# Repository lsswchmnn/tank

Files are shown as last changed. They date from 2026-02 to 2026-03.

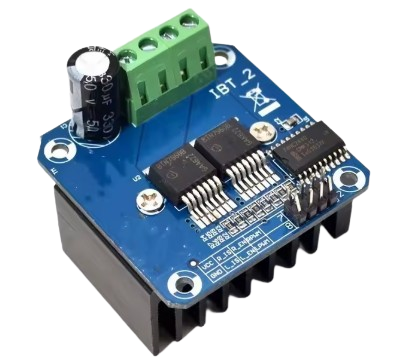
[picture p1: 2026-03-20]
Präsentation/h_brücke.png

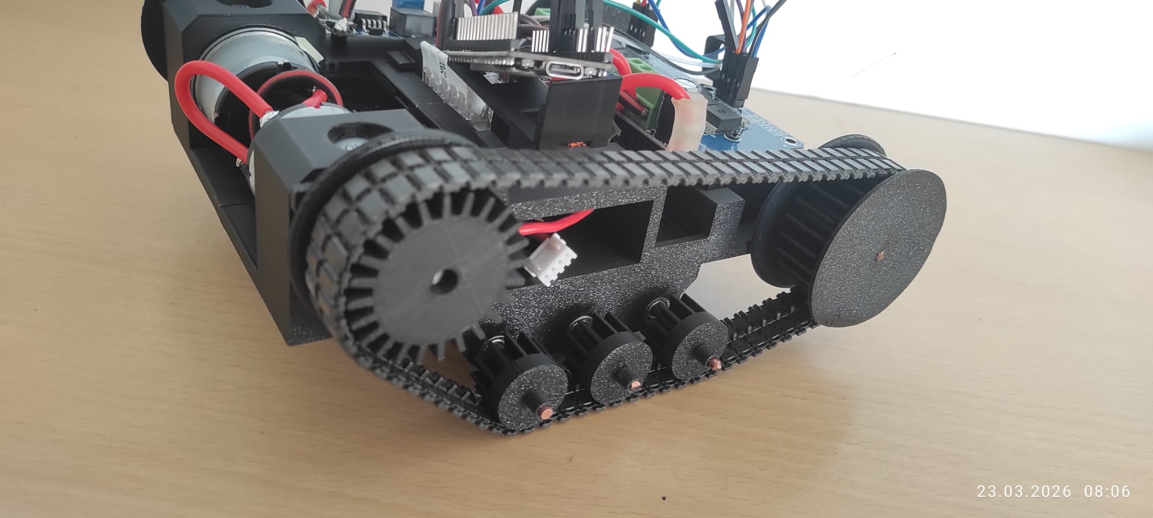
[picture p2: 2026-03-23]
Präsentation/WhatsApp Image 2026-03-23 at 09.37.09.jpeg

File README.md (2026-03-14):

# RC-Panzer

## Zeitplan:

12.Feb. - 27.März: Arbeit an (ca. 4 Wochen (exkl. Ferien)

16. März: Austausch zum Stand der Projekte, Problembesprechung

23. März: Präsentation / Abgabe des Semesterprojektes 

## ToDo:

- Teile bestellen

- 3D-Modell erstellen

- Schaltplan erstellen

- Lauffähiges Grundmodell bauen

## Weitere Teile:

- ESP32(1x 4,69 EUR),
- Motordriver (2x ins.: 6,98 EUR), 
- BUCK-Converter (2x ins.: 1,89 EUR), 
- Motoren (2x ins.: 13,89 EUR), 
- Akku(1x 17,49 EUR) 

### == 46,03 EUR (Bezahlt)

- AWG 14 Kabel (1x 1,75 EUR),
- 3x200mm Metallachsen (1x 4,48EUR),
- 20pcs Kugellager (1x 2,09 EUR)

### == 8,32 EUR (nicht bezahlt) 

- Wago Klemmen == 4,20 EUR (nicht bezahlt) 
- Ketten == 10,98 EUR (nicht bezahlt)
- Jumperkabel == 5,94 EUR (nicht bezahlt)

### == 21,12 EUR (nicht bezahlt)

- 3x300mm (1x 3,12 EUR)
- Schrumpfschläuche 164 pcs. (1x 2,79 EUR)
- AWG 14 Kabel (1x 3,31 EUR)

### == 9, 22 EUR (nicht bezahlt)

## INSGESAMT: 84,69 EUR

- Panzerketten: https://www.modellbau-seidel.de/index.php?firma=Tamiya&best=0003778 (1,7cm x 42,5cm) ODER https://www.modellbau-seidel.de/index.php?firma=Tamiya&best=0443086 (1,5cm x 35cm)

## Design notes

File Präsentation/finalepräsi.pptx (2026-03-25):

## Kettenfahrzeug

Semesterprojekt von Lasse, Hossein, Julian

## Inhaltsverzeichnis

1. Konstruktion und Planung
2. Elektronik und Verkabelung
3. Programmierung
4. Allgemeines

## Konstruktion

Lasse

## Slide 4

Rahmen

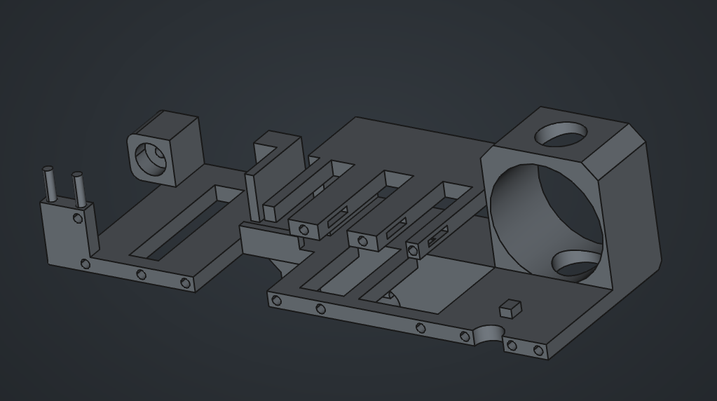
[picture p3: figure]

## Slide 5

Weitere Teile

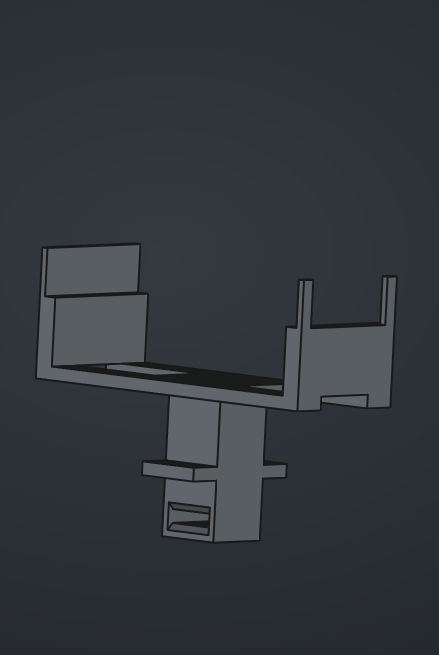
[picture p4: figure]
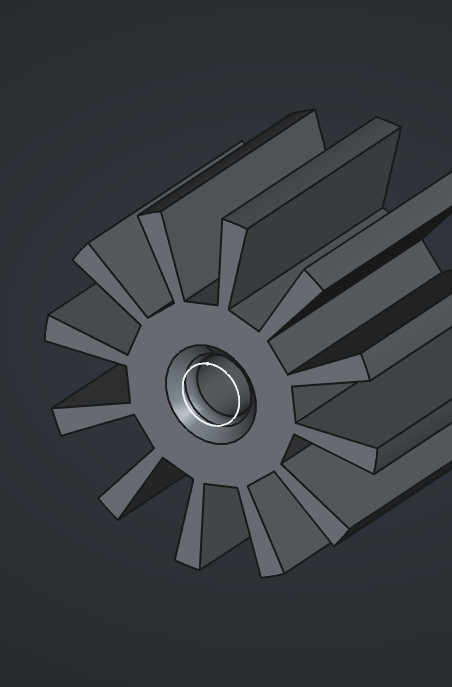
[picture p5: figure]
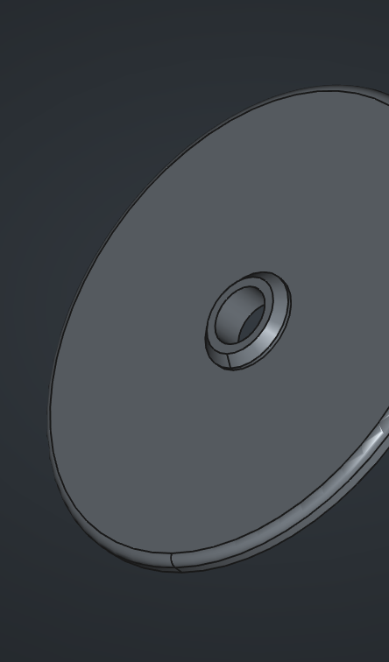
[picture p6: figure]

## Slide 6

Kabelmanagement

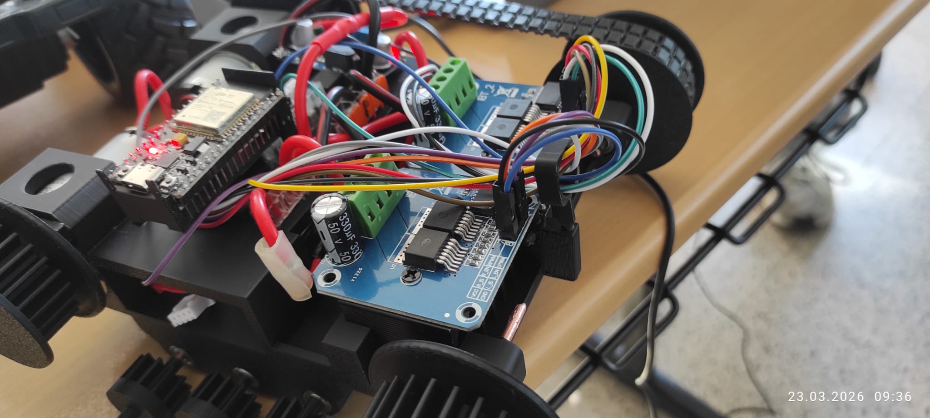
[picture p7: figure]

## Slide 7

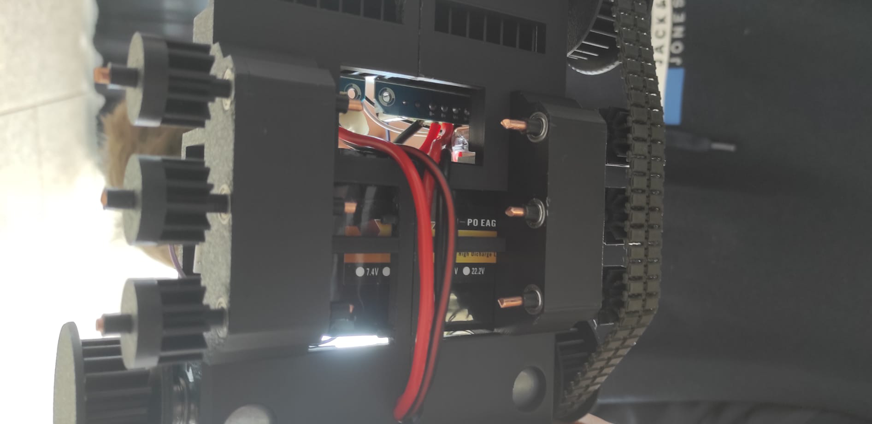
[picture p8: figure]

Kabelmanagement

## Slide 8

Fahrgestell

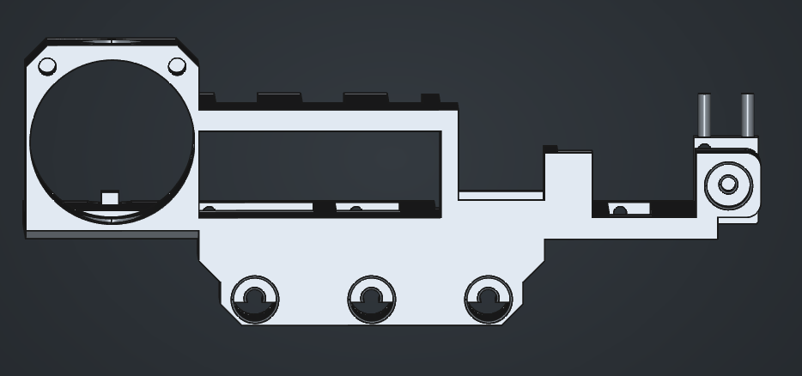
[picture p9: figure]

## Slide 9

Fahrgestell


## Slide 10

Zwischenfazit

Negativ
- Viele Testdrucke notwendig (Material- und Zeitaufwand)
- Millimeter können ein Modell unbrauchbar machen

Positiv
- Doppeltes Fahrgestell
- Modulares System mit vielen externen Teilen
- Flexibilität des Materials ist ein Vorteil

Allgemein
- Frühe durchdachte Planung lohnt sich
- 3D-Druck-Ungenauigkeiten antizipieren
- Improvisation ist oft notwendig

## Elektronik

Julian

## Elektronik

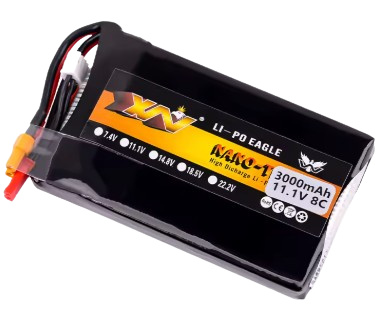
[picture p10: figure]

- 11.1V 3500mAh - Akku
- 2x BTS7960 43A – H-Brücke
- 2x JGB37-520 12V Motor
- LM2596 – Buck-Converter
- ESP32 Dev-Module (38 Pins)

*Alle aufgeführten Bauteile stammen von Aliexpress

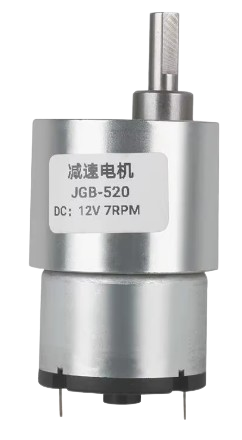
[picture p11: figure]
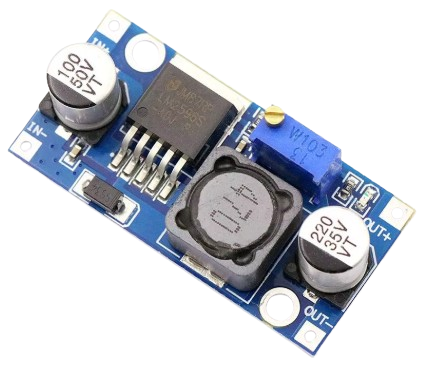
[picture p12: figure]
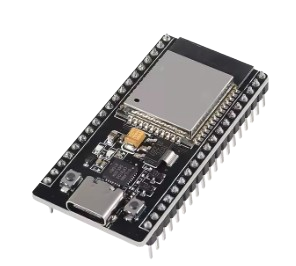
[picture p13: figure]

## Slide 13

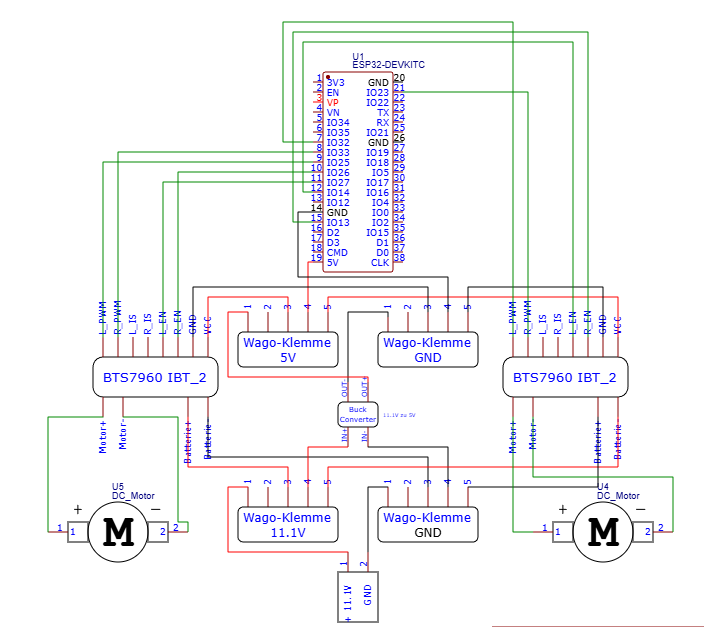
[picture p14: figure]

https://easyeda.com

## Programmierung

Hossein

## Programmierung

1. Mit ChatGPT ein Überblick erstellt (nötige Tools usw.)
2. Verbindung zwischen ESP32 und PS5 Controller (Bluepad32)
3. Schnittstelle zwischen Elektronik und Code

## 1. Schritt

1. Ziel definiert: Was soll der Roboter können?
2. KI gefragt (z.B. ChatGPT/Claude): Weche Komponenten brauche ich? Welche Bibliotheken? Welcher Ansatz?
3. Grobe Architektur skizziert: ESP32 -> Bluetooth -> PS5 Controller -> Motorsteuerung
4. Offene Fragen gesammelt: Was muss ich noch recherchieren?

## 2. Schritt

1. Youtube & Dokumentation (Bluepad32) als Einstieg
2. Ersten Prototyp erstellt & getestet
3. Stabile BT-Verbindung ohne MAC-Adresse
4. Alle Eingaben live auslesbar (Buttons, Achsen, Trigger)
5. Problem erkannt: Stick Drift / Rauschen bei Nullstellung
6. Lösung: Deadzone + Komplettauslenkung definiert

## 3. Schritt

1. Verbindungs-Code als Basis genommen & erweitert
2. Achsenwerte auf Motorgeschwindigkeit gemappt
3. Deadzone -> Motoren stehen still
4. Komplettauslenkung -> Maximale Motorleistung
5. Richtungssteuerung implementiert

## Code

1. Bibliotheken einbinden
2. Konstanten definieren
3. Controller Array
4. Callback Funktion
5. Setup()
6. Loop()

## Bibliotheken

Bluepad32.h :
Übernahme der Bluetooth Protokolle

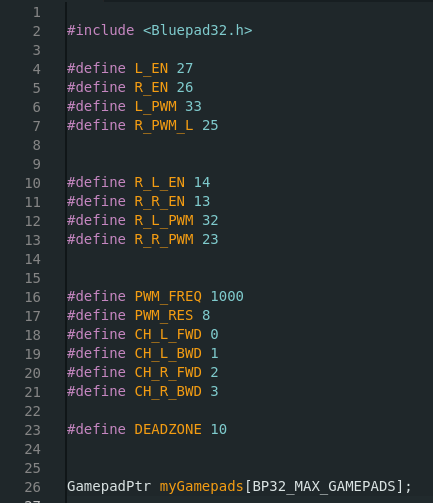
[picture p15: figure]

## Konstanten definieren

Definition:
- Verbindung BTS7960 mit ESP32
- PWM Frequenz
- PWM Resolution
- LEDC Kanäle
- Deadzone

## Controller Array

Gameptr-> Pointer
- Speicheradresse der Controller Daten
BP32_MAX_GAMEPADS
- Array

## Callback Funktion

- Aufruf der Funktion -> Controller verbunden
- FoundEmptySlot -> Reminder
- Zählschleife
- Nullptr -> Nullpointer
- Aufruf der Eigenschaften des Controllers
- Controller gefunden-> Schleife wird beendet

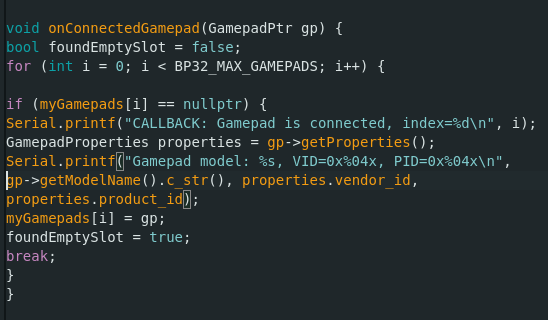
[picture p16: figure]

## Callback Funktion

- prüft ob der Slot gefunden wurde
- Slot wird geleert
- Schleife beendet

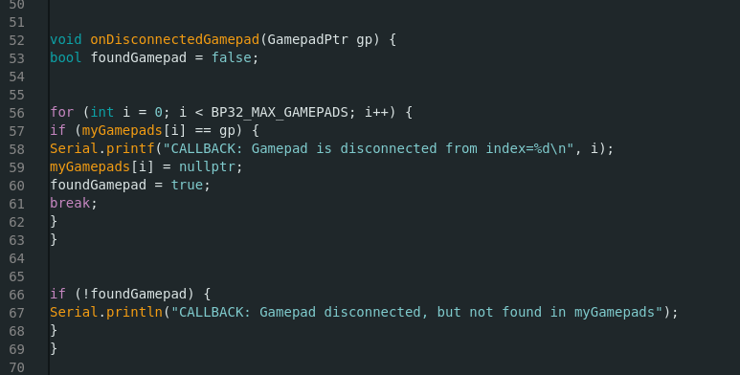
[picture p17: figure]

## Setup()

- Speichert wenn sich der Controller verbindet/ trennt

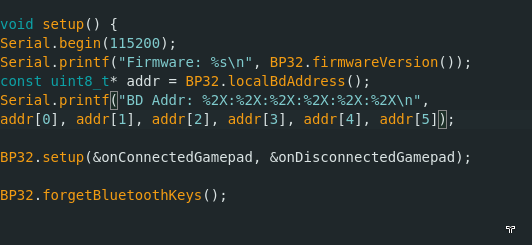
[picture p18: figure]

## PINS, PWM & LEDC

- Pin 27 als Ausgang
  - Setzt Pin auf HIGH(3,3V)
- LEDC Kanäle werden konfiguriert
- Kanal 0 wird mit Pin 33 verbunden

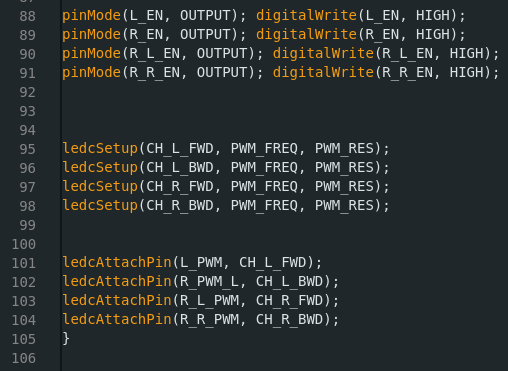
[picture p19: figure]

## loop

- ständiges Update
- Nach belegten Slot suchen -> Umbennenung -> myGamepad
- Doppelprüfung
  - Controller im Slot
  - Controller verbunden
- Werte aus den Sticks ablesen -> Methode axis -> myGamepad

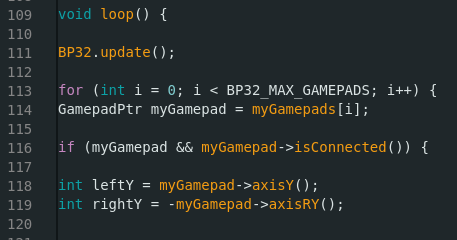
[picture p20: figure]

## Motorsteuerung

- Werte von Controller in PWM Werte umwandeln
- Vorwärts
  - CH_L_FWD speed
- Rückwärts
  - CH_L_BWD speed

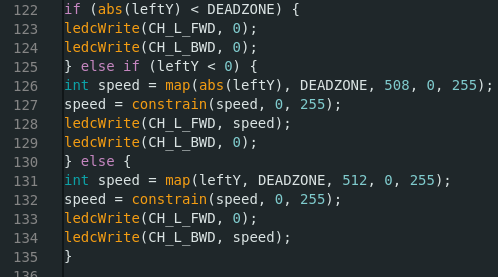
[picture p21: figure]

## Allgemeines

## Allgemeines

- Github als Kommunikationsplattform
- Ungelöste Probleme
- Arbeitsteilung

## Quellen

Code Dokumentation:
https://bluepad32.readthedocs.io/en/latest/plat_arduino/
Zusätzliche Board URL‘s:
https://raw.githubusercontent.com/espressif/arduino-esp32/gh-pages/package_esp32_index.json
https://raw.githubusercontent.com/ricardoquesada/esp32-arduino-lib-builder/master/bluepad32_files/package_esp32_bluepad32_index.json

## PWM und LEDC

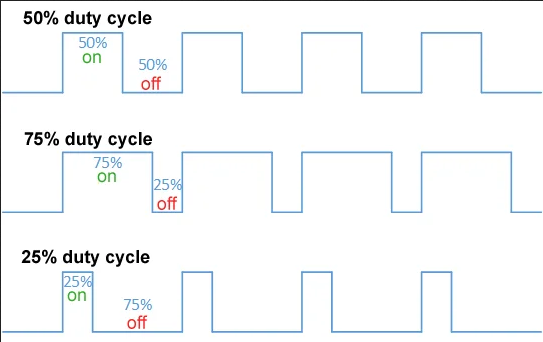
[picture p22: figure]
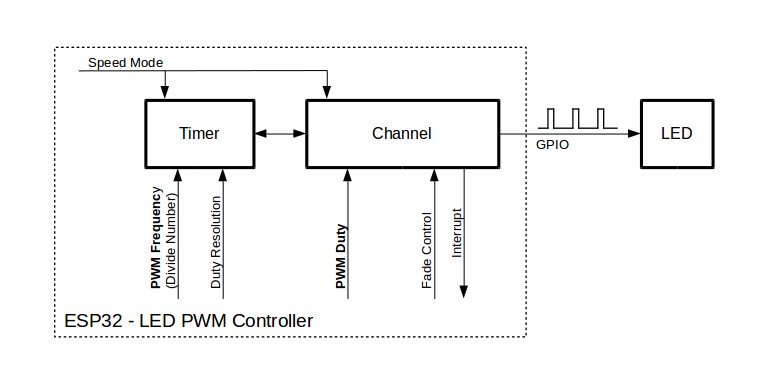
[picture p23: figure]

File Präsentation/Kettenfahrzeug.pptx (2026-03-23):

## Kettenfahrzeug

Semesterprojekt von Lasse, Hossein, Julian

## Inhaltsverzeichnis

1. Konstruktion und Planung
2. Elektronik und Verkabelung
3. Programmierung
4. Allgemeines

## Konstruktion

Lasse

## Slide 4

Rahmen


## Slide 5

Weitere Teile


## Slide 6

Kabelmanagement


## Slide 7


Kabelmanagement

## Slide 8

Fahrgestell


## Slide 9

Fahrgestell


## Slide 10

Zwischenfazit

Negativ
- Viele Testdrucke notwendig (Material- und Zeitaufwand)
- Millimeter können ein Modell unbrauchbar machen

Positiv
- Doppeltes Fahrgestell
- Modulares System mit vielen externen Teilen
- Flexibilität des Materials ist ein Vorteil

Allgemein
- Frühe durchdachte Planung lohnt sich
- 3D-Druck-Ungenauigkeiten antizipieren
- Improvisation ist oft notwendig

## Elektronik

Julian

## Elektronik


- 11.1V 3500mAh - Akku
- 2x BTS7960 43A – H-Brücke
- 2x JGB37-520 12V Motor
- LM2596 – Buck-Converter
- ESP32 Dev-Module (38 Pins)

*Alle aufgeführten Bauteile stammen von Aliexpress


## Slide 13


https://easyeda.com

## Programmierung

Hossein

## Programmierung

1. Mit ChatGPT ein Überblick erstellt (nötige Tools usw.)
2. Verbindung zwischen ESP32 und PS5 Controller (Bluepad32)
3. Schnittstelle zwischen Elektronik und Code

## 1. Schritt

1. Ziel definiert: Was soll der Roboter können?
2. KI gefragt (z.B. ChatGPT/Claude): Weche Komponenten brauche ich? Welche Bibliotheken? Welcher Ansatz?
3. Grobe Architektur skizziert: ESP32 -> Bluetooth -> PS5 Controller -> Motorsteuerung
4. Offene Fragen gesammelt: Was muss ich noch recherchieren?

## 2. Schritt

1. Youtube & Dokumentation (Bluepad32) als Einstieg
2. Ersten Prototyp erstellt & getestet
3. Stabile BT-Verbindung ohne MAC-Adresse
4. Alle Eingaben live auslesbar (Buttons, Achsen, Trigger)
5. Problem erkannt: Stick Drift / Rauschen bei Nullstellung
6. Lösung: Deadzone + Komplettauslenkung definiert

## 3. Schritt

1. Verbindungs-Code als Basis genommen & erweitert
2. Achsenwerte auf Motorgeschwindigkeit gemappt
3. Deadzone -> Motoren stehen still
4. Komplettauslenkung -> Maximale Motorleistung
5. Richtungssteuerung implementiert

## Code

1. Bibliotheken einbinden
2. Konstanten definieren
3. Controller Array
4. Callback Funktion
5. Setup()
6. Loop()

## Bibliotheken

#include <Bluepad32.h>

## Konstanten definieren

#define L_EN 27

#define R_EN 26

#define L_PWM 33

#define R_PWM_L 25

#define R_L_EN 14

#define R_R_EN 13

#define R_L_PWM 32

##define R_R_PWM 23

#define PWM_FREQ 1000

#define PWM_RES 8

#define CH_L_FWD 0

#define CH_L_BWD 1

#define CH_R_FWD 2

#define CH_R_BWD 3

#define DEADZONE 10

## Controller Array

GamepadPtr myGamepads[BP32_MAX_GAMEPADS];

## Callback Funktion

- Alle 4 Slots im Array durchsuchen
- Ersten leeren Slot (nullptr) suchen
- Controller-Pointer in den freien Slot eintragen
- Falls kein freier Slot → Fehlermeldung im Serial Monitor ausgeben

## Setup()

- Serielle Kommunikation starten (Serial Monitor)
- Firmware-Version und Bluetooth-Adresse des ESP32 ausgeben
- Bluetooth-Callbacks bei Bluepad32 registrieren
- Alte Bluetooth-Paarungsschlüssel löschen
- Enable-Pins der beiden BTS7960 auf OUTPUT setzen und dauerhaft HIGH schalten
- LEDC-Kanäle konfigurieren (Frequenz + Auflösung)
- LEDC-Kanäle mit den physischen Pins verbinden

## Loop()

- Joystick-Werte des linken und rechten Sticks auslesen
- Deadzone prüfen — wenn Stick in der Mitte → Motor stop
- Richtung bestimmen — negativ = vorwärts, positiv = rückwärts
- Joystick-Wert mit map() auf PWM-Bereich 0–255 skalieren
- PWM-Wert mit constrain() absichern
- PWM-Signal per ledcWrite() auf den Motor schreiben

## Allgemeines

## Allgemeines

- Github als Kommunikationsplattform
- Ungelöste Probleme
- Arbeitsteilung

## Quellen

Code Dokumentation:
https://bluepad32.readthedocs.io/en/latest/plat_arduino/
Zusätzliche Board URL‘s:
https://raw.githubusercontent.com/espressif/arduino-esp32/gh-pages/package_esp32_index.json
https://raw.githubusercontent.com/ricardoquesada/esp32-arduino-lib-builder/master/bluepad32_files/package_esp32_bluepad32_index.json

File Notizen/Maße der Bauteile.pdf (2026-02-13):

## Maße der Bauteile

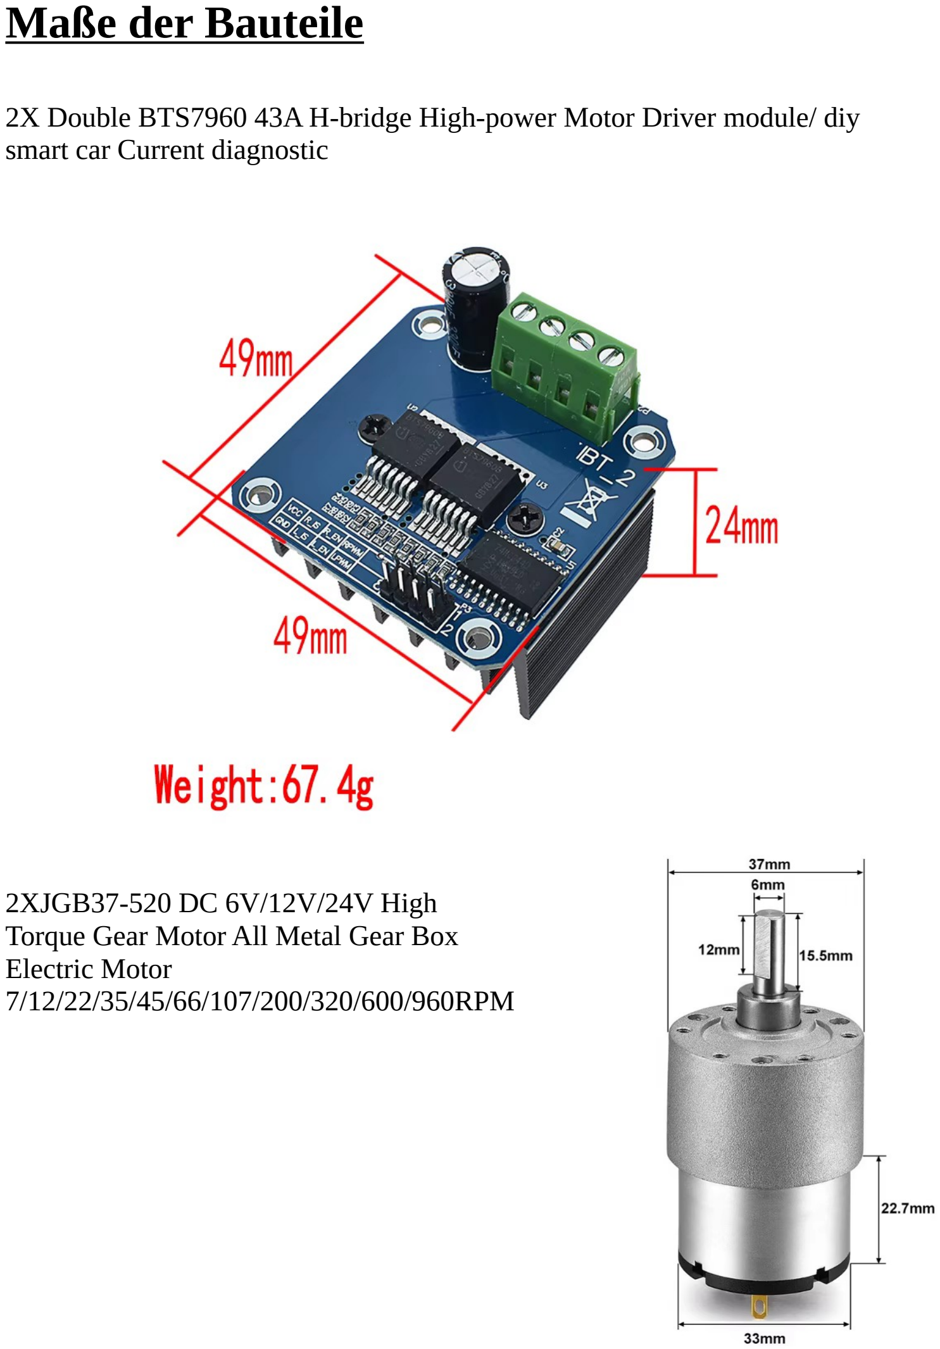
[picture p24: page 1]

2X Double BTS7960 43A H-bridge High-power Motor Driver module/ diy smart car Current diagnostic

2XJGB37-520 DC 6V/12V/24V High Torque Gear Motor All Metal Gear Box Electric Motor
7/12/22/35/45/66/107/200/320/600/960RPM

1X DC-DC Buck Step Down Module LM2596 DC/DC 4.0~40V to 1.25-37V Adjustable Voltage Regulator With LED Voltmeter

length 54mm width 23mm height 18mm (Von Aliexpress)

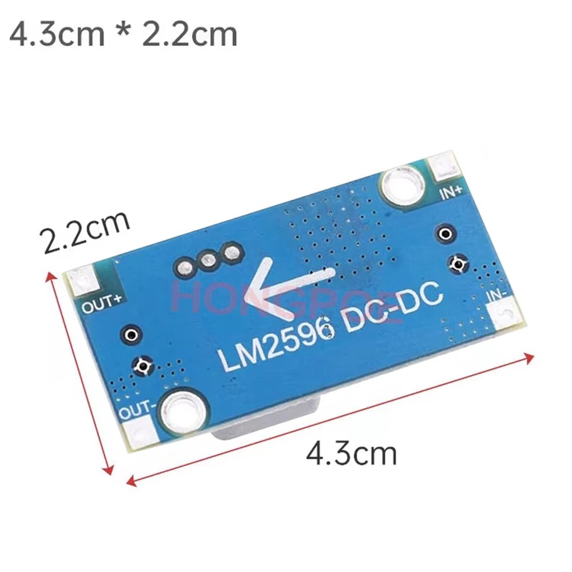
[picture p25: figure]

(von AliBABA)

1X ESP32 CP2102 38Pin 4MB Development Board WiFi+Bluetooth Ultra-Low Power Consumption Dual Core
55.0mm (including USB socket) x 27.5mm x 13.0mm (including header pins)

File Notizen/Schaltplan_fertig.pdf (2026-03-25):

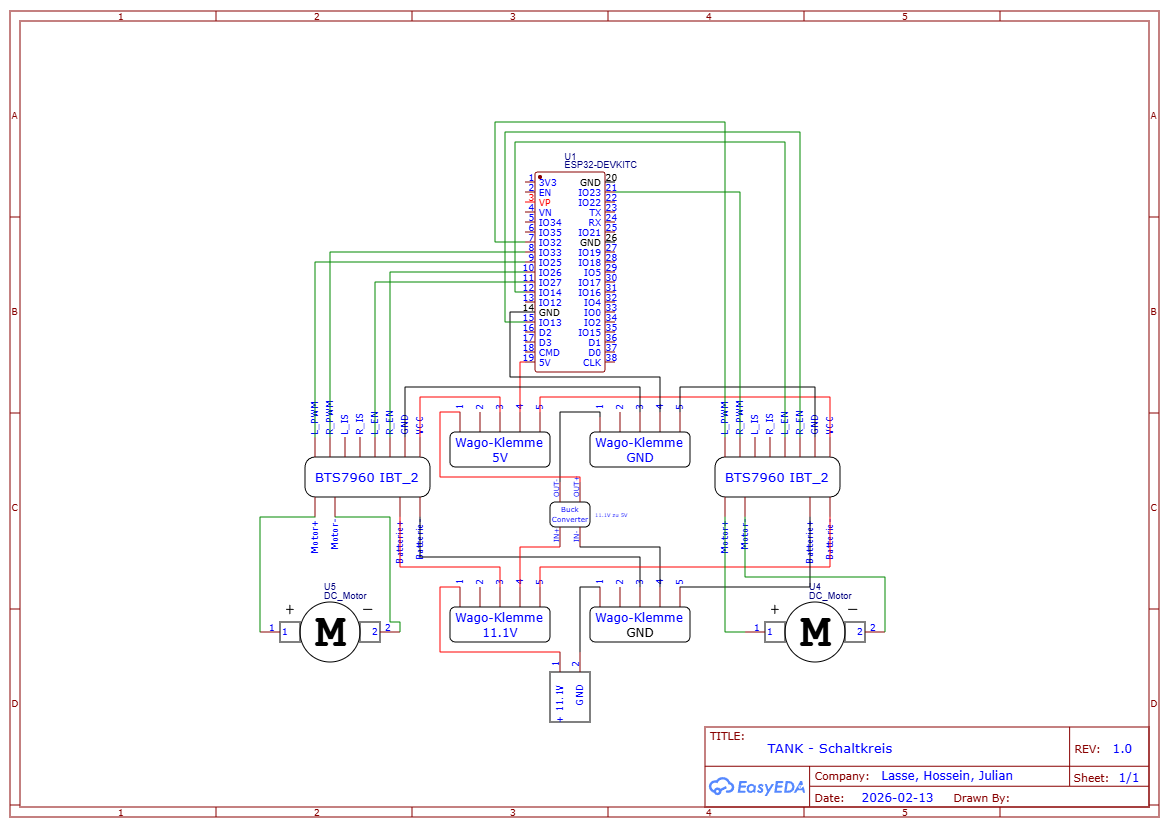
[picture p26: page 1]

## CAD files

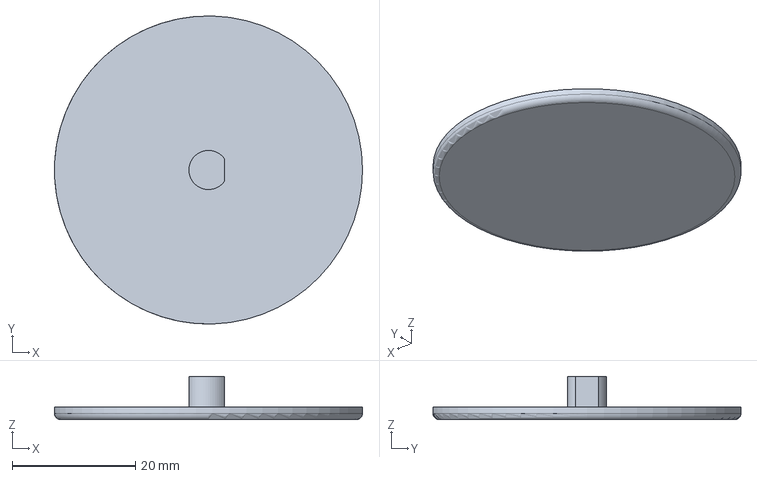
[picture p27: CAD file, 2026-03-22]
3D-Druck/freecad-dateien/stützrad_außen.FCStd
50.0 x 50.0 x 7.00 mm

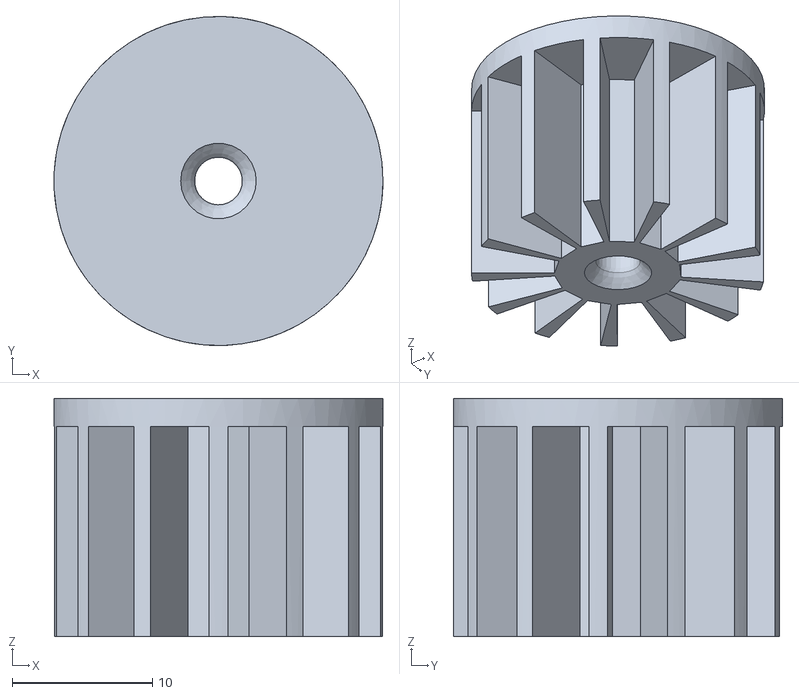
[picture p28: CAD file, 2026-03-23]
3D-Druck/stl-dateien/stützrad_neu.stl
23.5 x 23.5 x 17.0

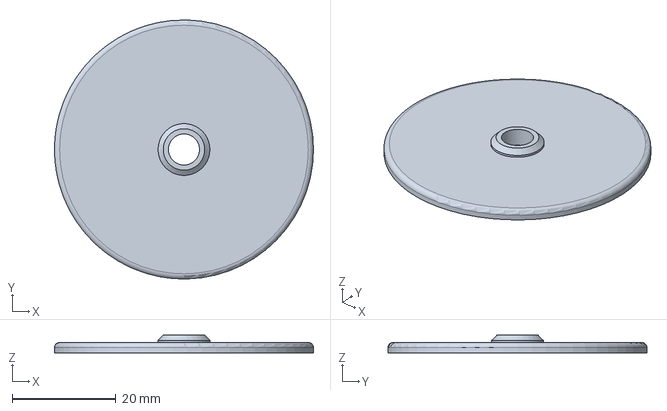
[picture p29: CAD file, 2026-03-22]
3D-Druck/freecad-dateien/stütz_scheibe_vorne.FCStd
50.0 x 50.0 x 3.40 mm

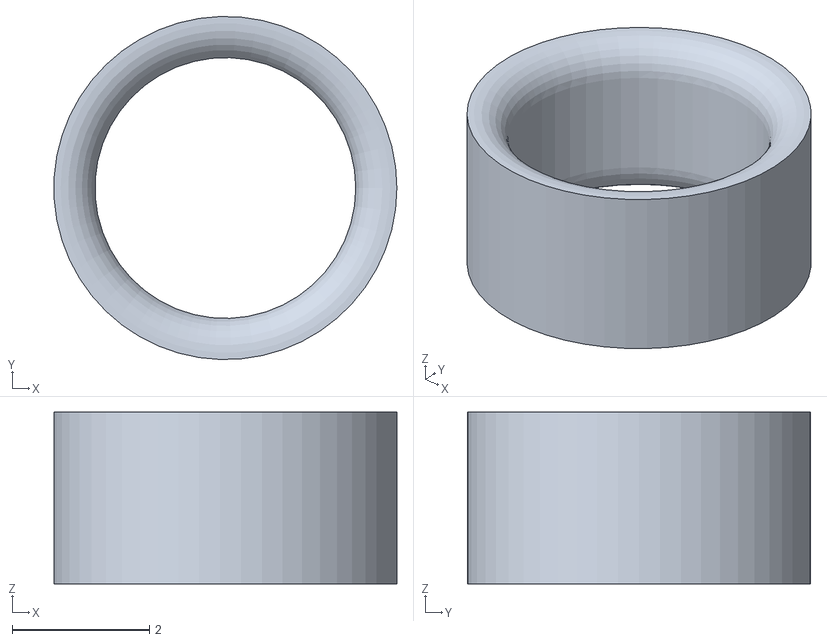
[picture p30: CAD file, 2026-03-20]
3D-Druck/stl-dateien/achse_halterung_klein.stl
5.00 x 5.00 x 2.50

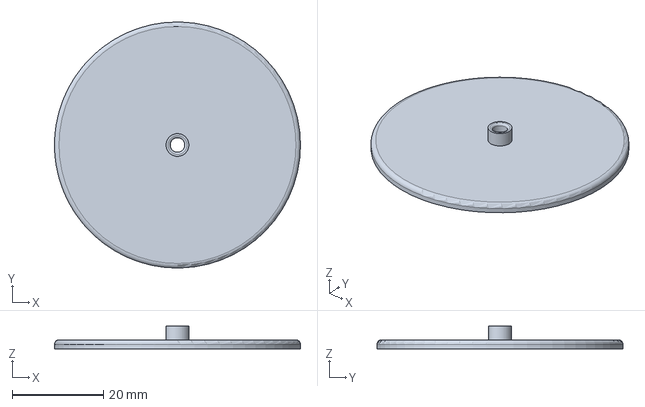
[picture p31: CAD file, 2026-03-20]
3D-Druck/freecad-dateien/stütz_scheibe_hinten.FCStd
54.0 x 54.0 x 5.00 mm

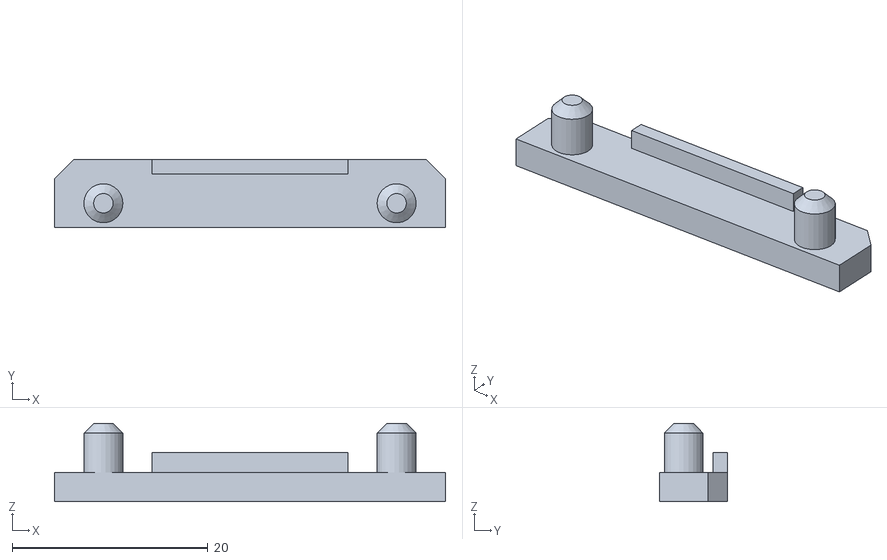
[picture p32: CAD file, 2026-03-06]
3D-Druck/stl-dateien/motor_stütze_3.stl
40.0 x 7.00 x 8.00

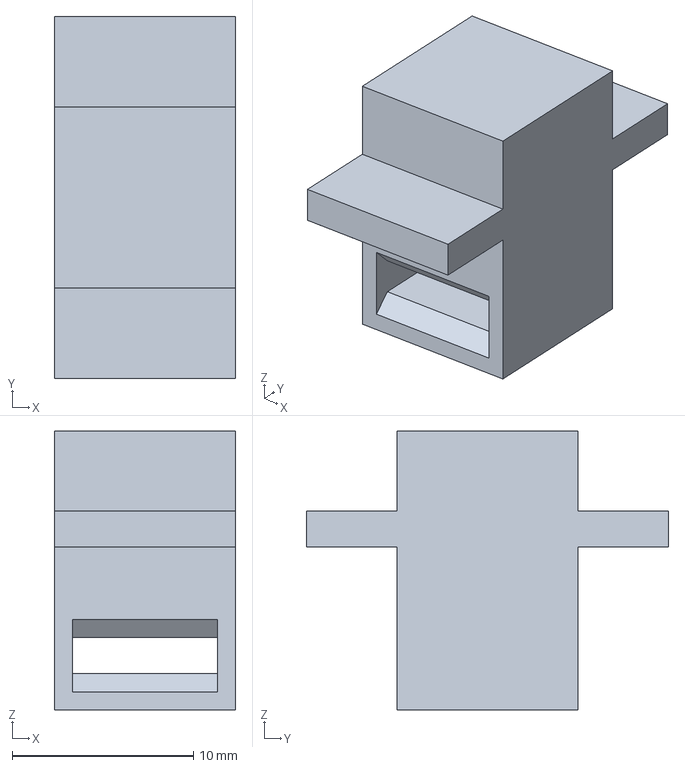
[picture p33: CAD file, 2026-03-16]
3D-Druck/freecad-dateien/block.FCStd
10.0 x 20.0 x 15.4 mm

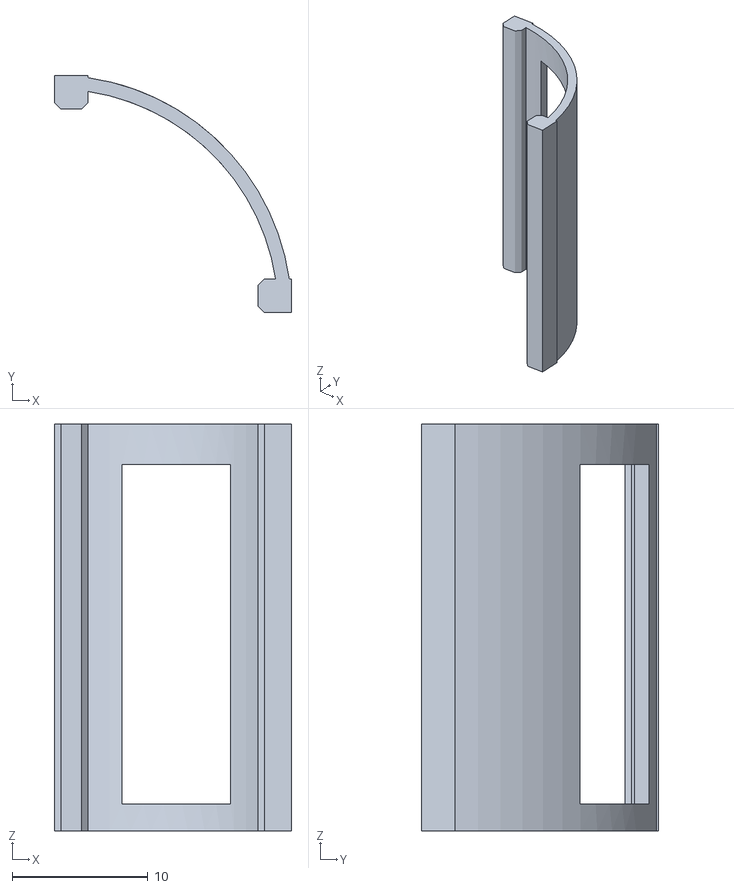
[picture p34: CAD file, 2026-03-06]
3D-Druck/stl-dateien/motor_verbindung_neu.stl
17.5 x 17.5 x 30.0

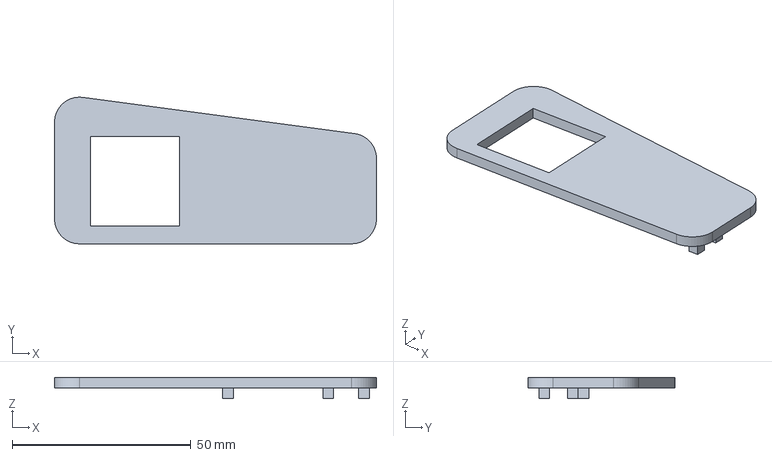
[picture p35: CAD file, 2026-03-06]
3D-Druck/freecad-dateien/seitenverkleidung_links.FCStd
90.0 x 41.0 x 6.00 mm

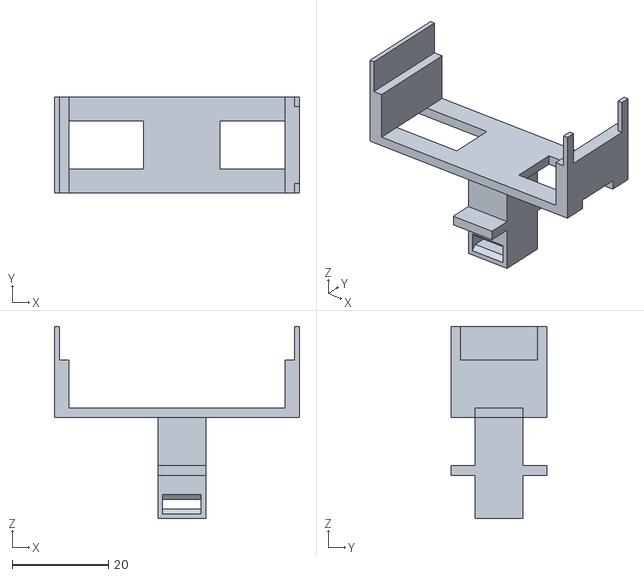
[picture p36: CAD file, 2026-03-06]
3D-Druck/stl-dateien/esp32_halterung_neu.stl
51.0 x 20.0 x 40.0

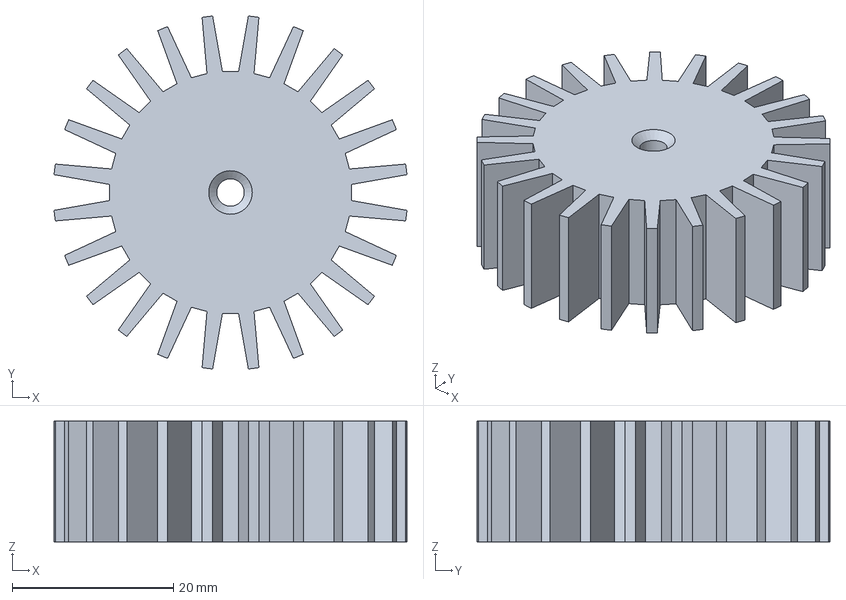
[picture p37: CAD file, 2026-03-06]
3D-Druck/freecad-dateien/stützrad_hinten.FCStd
43.8 x 43.8 x 15.0 mm

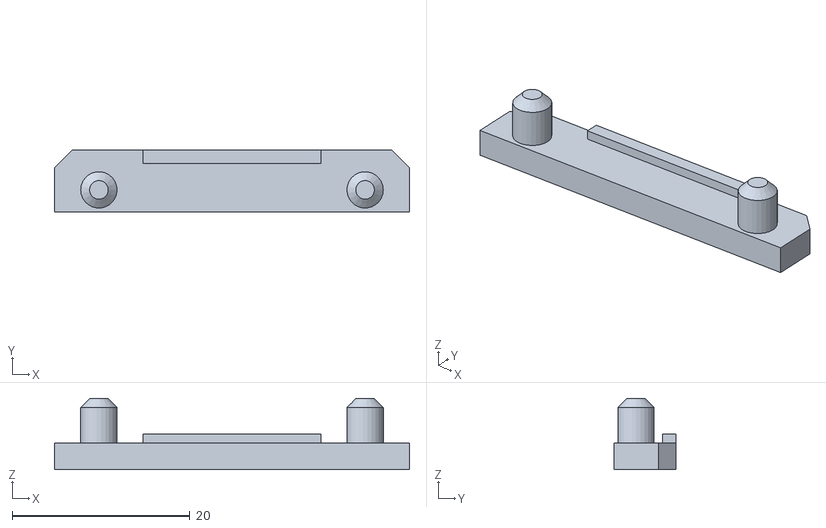
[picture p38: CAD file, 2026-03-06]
3D-Druck/stl-dateien/motor_stütze_2.stl
40.0 x 7.00 x 8.00

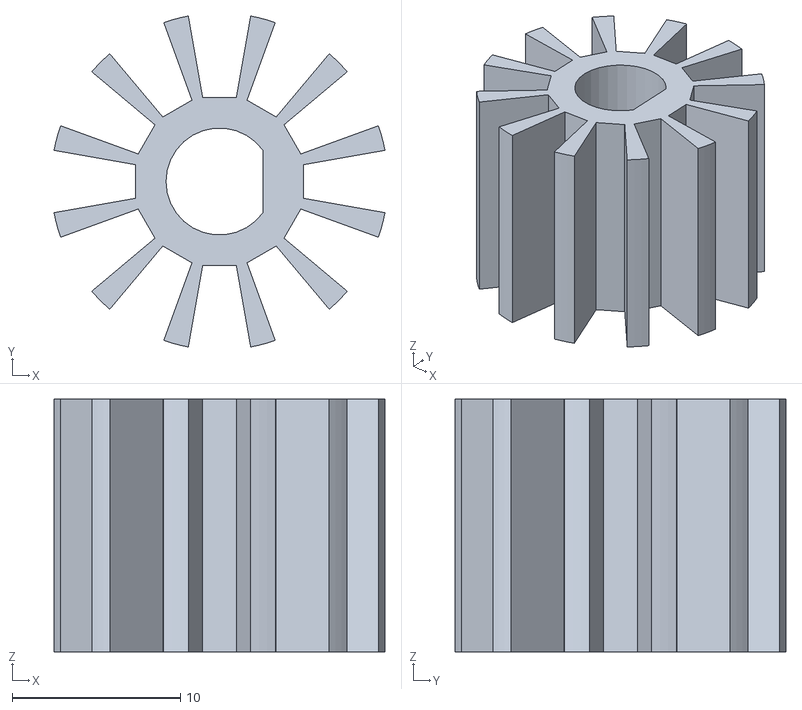
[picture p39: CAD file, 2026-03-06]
3D-Druck/stl-dateien/triebrad_neu.stl
19.7 x 19.7 x 15.0

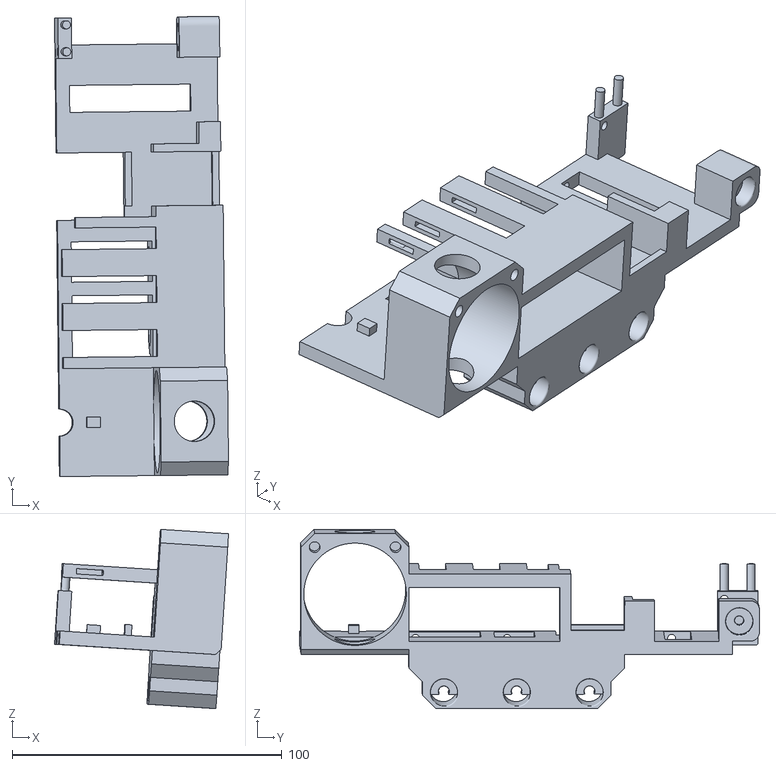
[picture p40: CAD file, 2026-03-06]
3D-Druck/stl-dateien/rahmen_links_neu.stl
64.5 x 170.6 x 66.5

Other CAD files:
3D-Druck/stl-dateien/stütz_scheibe_hinten_final.stl
3D-Druck/freecad-dateien/achse_halterung.FCStd
3D-Druck/freecad-dateien/motor_stütze.FCStd
3D-Druck/freecad-dateien/motor_verbindung.FCStd
3D-Druck/freecad-dateien/alt/brett_stl_halterung.FCStd
3D-Druck/freecad-dateien/alt/deckel.FCStd
3D-Druck/freecad-dateien/alt/esp32_halterung.FCStd
3D-Druck/freecad-dateien/alt/kabelführung.FCStd
3D-Druck/freecad-dateien/alt/motor_stütze.FCStd
3D-Druck/freecad-dateien/alt/motor_verbindung.FCStd
3D-Druck/freecad-dateien/alt/stützrad.FCStd
3D-Druck/freecad-dateien/alt/test_halterung.FCStd
3D-Druck/freecad-dateien/alt/test_löcher.FCStd
3D-Druck/freecad-dateien/alt/triebrad_2.FCStd
3D-Druck/freecad-dateien/alt/triebrad_groß.FCStd
3D-Druck/freecad-dateien/brett_stl_halterung.FCStd
3D-Druck/freecad-dateien/deckel.FCStd
3D-Druck/freecad-dateien/kabelführung.FCStd
3D-Druck/freecad-dateien/rahmen_neu.FCStd
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

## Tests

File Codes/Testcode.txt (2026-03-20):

/*
 * ESP32 Motor-Test für 2x BTS7960 H-Brücken
 * Motoren: JGB37-520 (107 RPM)
 */

// Definition der Pins - Linker Motor
const int L_MOTOR_R_EN = 26;
const int L_MOTOR_L_EN = 27;
const int L_MOTOR_R_PWM = 25;
const int L_MOTOR_L_PWM = 33;

// Definition der Pins - Rechter Motor
const int R_MOTOR_R_EN = 13;
const int R_MOTOR_L_EN = 14;
const int R_MOTOR_R_PWM = 23;
const int R_MOTOR_L_PWM = 32;

// PWM Einstellungen für den ESP32
const int freq = 5000;
const int resolution = 8; // 0-255

void setup() {
  Serial.begin(115200);
  Serial.println("Motor-Test startet...");

  // Alle Pins als Ausgang definieren
  pinMode(L_MOTOR_R_EN, OUTPUT);
  pinMode(L_MOTOR_L_EN, OUTPUT);
  pinMode(L_MOTOR_R_PWM, OUTPUT);
  pinMode(L_MOTOR_L_PWM, OUTPUT);

  pinMode(R_MOTOR_R_EN, OUTPUT);
  pinMode(R_MOTOR_L_EN, OUTPUT);
  pinMode(R_MOTOR_R_PWM, OUTPUT);
  pinMode(R_MOTOR_L_PWM, OUTPUT);

  // Aktiviere beide H-Brücken (Enable-Pins auf HIGH)
  digitalWrite(L_MOTOR_R_EN, HIGH);
  digitalWrite(L_MOTOR_L_EN, HIGH);
  digitalWrite(R_MOTOR_R_EN, HIGH);
  digitalWrite(R_MOTOR_L_EN, HIGH);

  Serial.println("H-Brücken aktiviert.");
}

void loop() {
  // --- TEST 1: Vorwärts (beide Motoren) ---
  Serial.println("Beide Motoren: Vorwärts (50% Speed)");
  analogWrite(L_MOTOR_R_PWM, 256); // Linker Motor Seite R
  analogWrite(L_MOTOR_L_PWM, 0);
  analogWrite(R_MOTOR_R_PWM, 256); // Rechter Motor Seite R
  analogWrite(R_MOTOR_L_PWM, 0);
  delay(3000);

  // Stopp
  stopMotors();
  delay(1000);

  // --- TEST 2: Rückwärts (beide Motoren) ---
  Serial.println("Beide Motoren: Rückwärts (50% Speed)");
  analogWrite(L_MOTOR_R_PWM, 0);
  analogWrite(L_MOTOR_L_PWM, 256); // Linker Motor Seite L
  analogWrite(R_MOTOR_R_PWM, 0);
  analogWrite(R_MOTOR_L_PWM, 256); // Rechter Motor Seite L
  delay(3000);

  // Stopp
  stopMotors();
  delay(2000);
}

// Hilfsfunktion zum Stoppen beider Motoren
void stopMotors() {
  Serial.println("Stopp...");
  analogWrite(L_MOTOR_R_PWM, 0);
  analogWrite(L_MOTOR_L_PWM, 0);
  analogWrite(R_MOTOR_R_PWM, 0);
  analogWrite(R_MOTOR_L_PWM, 0);
}

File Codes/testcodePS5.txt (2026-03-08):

#include <ps5Controller.h>

// Pins für Motor Links (BTS7960)
const int L_MOTOR_LEN = 27;
const int L_MOTOR_REN = 26;
const int L_MOTOR_RPWM = 33; // Vorwärts
const int L_MOTOR_LPWM = 25; // Rückwärts

// Pins für Motor Rechts (BTS7960)
const int R_MOTOR_LEN = 14;
const int R_MOTOR_REN = 13;
const int R_MOTOR_RPWM = 23; // Vorwärts
const int R_MOTOR_LPWM = 32; // Rückwärts

// PWM Einstellungen
const int freq = 5000;
const int resolution = 8; // 0-255

// Kanäle für ESP32 PWM (LEDC)
const int chanL_F = 0;
const int chanL_B = 1;
const int chanR_F = 2;
const int chanR_B = 3;

bool emergencyStop = false;

void setup() {
  Serial.begin(115200);

  // Pin-Modi setzen
  pinMode(L_MOTOR_LEN, OUTPUT);
  pinMode(L_MOTOR_REN, OUTPUT);
  pinMode(R_MOTOR_LEN, OUTPUT);
  pinMode(R_MOTOR_REN, OUTPUT);

  // Enable-Pins auf HIGH setzen (H-Brücken aktiv)
  digitalWrite(L_MOTOR_LEN, HIGH);
  digitalWrite(L_MOTOR_REN, HIGH);
  digitalWrite(R_MOTOR_LEN, HIGH);
  digitalWrite(R_MOTOR_REN, HIGH);

  // PWM Kanäle konfigurieren
  ledcSetup(chanL_F, freq, resolution);
  ledcSetup(chanL_B, freq, resolution);
  ledcSetup(chanR_F, freq, resolution);
  ledcSetup(chanR_B, freq, resolution);

  // PWM Kanäle an Pins binden
  ledcAttachPin(L_MOTOR_RPWM, chanL_F);
  ledcAttachPin(L_MOTOR_LPWM, chanL_B);
  ledcAttachPin(R_MOTOR_RPWM, chanR_F);
  ledcAttachPin(R_MOTOR_LPWM, chanR_B);

  // Motoren initial stoppen
  stopAllMotors();

  // PS5 Controller Verbindung starten (MAC-Adresse hier anpassen!)
  ps5.begin("00:11:22:33:44:55"); 
  Serial.println("Warte auf PS5 Controller Verbindung...");
}

void loop() {
  if (ps5.isConnected()) {
    
    // Notstopp-Logik (Kreis-Taste)
    if (ps5.Circle()) {
      emergencyStop = true;
      Serial.println("NOTSTOPP AKTIVIERT!");
    }

    if (emergencyStop) {
      stopAllMotors();
    } else {
      // Joystick-Werte abgreifen (-128 bis 127)
      // Wir nutzen nur die Y-Achsen für die Kettensteuerung (Tank-Drive)
      int leftY = ps5.LStickY();
      int rightY = ps5.RStickY();

      handleMotor(leftY, chanL_F, chanL_B);  // Linke Kette
      handleMotor(rightY, chanR_F, chanR_B); // Rechte Kette
    }
  } else {
    // Sicherheit: Stopp, wenn Verbindung abbricht
    stopAllMotors();
  }
}

/**
 * Hilfsmethode zur Steuerung eines Motors
 * @param stickValue Der Wert des Joysticks (-128 bis 127)
 * @param forwardChan LEDC Kanal für Vorwärts
 * @param backwardChan LEDC Kanal für Rückwärts
 */
void handleMotor(int stickValue, int forwardChan, int backwardChan) {
  int deadzone = 15; // Rauschen unterdrücken

  if (stickValue > deadzone) {
    // Vorwärts fahren
    int speed = map(stickValue, deadzone, 127, 0, 255);
    ledcWrite(forwardChan, speed);
    ledcWrite(backwardChan, 0);
  } 
  else if (stickValue < -deadzone) {
    // Rückwärts fahren
    int speed = map(abs(stickValue), deadzone, 128, 0, 255);
    ledcWrite(forwardChan, 0);
    ledcWrite(backwardChan, speed);
  } 
  else {
    // Stillstand
    ledcWrite(forwardChan, 0);
    ledcWrite(backwardChan, 0);
  }
}

/**
 * Schaltet alle PWM-Ausgänge ab
 */
void stopAllMotors() {
  ledcWrite(chanL_F, 0);
  ledcWrite(chanL_B, 0);
  ledcWrite(chanR_F, 0);
  ledcWrite(chanR_B, 0);
}

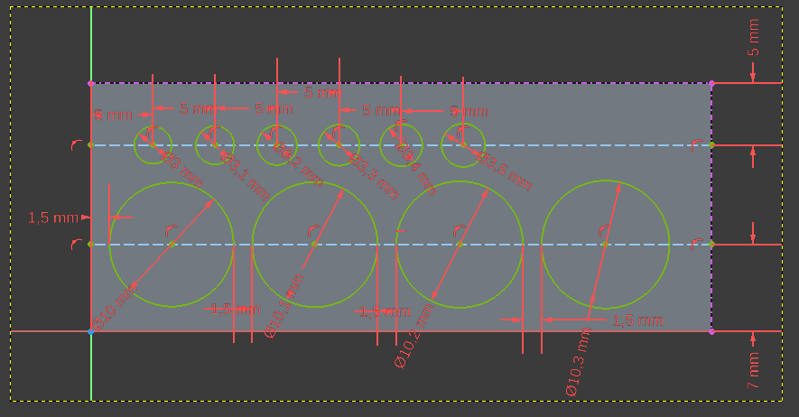
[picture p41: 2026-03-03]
Notizen/maße_test_löcher.png

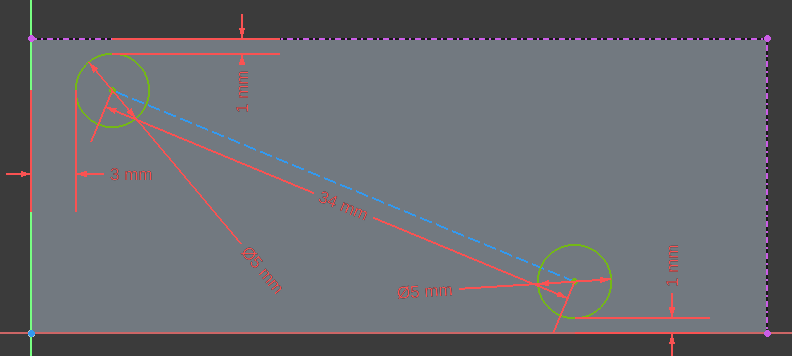
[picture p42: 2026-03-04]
Notizen/maße_test_halterung.png

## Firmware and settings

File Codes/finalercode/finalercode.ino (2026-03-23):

#include <Bluepad32.h>
//Pin-Definitionen
#define L_EN 27
#define R_EN 26
#define L_PWM 33
#define R_PWM_L 25 // R_PWM des linken BTS7960


#define R_L_EN 14
#define R_R_EN 13
#define R_L_PWM 32
#define R_R_PWM 23


// PWM-Kanal-Konfiguration (LEDC)
#define PWM_FREQ 1000 // Hz
#define PWM_RES 8 // Bit → 0-255
#define CH_L_FWD 0 // Kanal für L_PWM (vorwärts links)
#define CH_L_BWD 1 // Kanal für R_PWM_L (rückwärts links)
#define CH_R_FWD 2 // Kanal für R_L_PWM (vorwärts rechts)
#define CH_R_BWD 3 // Kanal für R_R_PWM (rückwärts rechts)


// Deadzone – hier selbst anpassen (0-511)
#define DEADZONE 10
GamepadPtr myGamepads[BP32_MAX_GAMEPADS];


// This callback gets called any time a new gamepad is connected.
// Up to 4 gamepads can be connected at the same time.
void onConnectedGamepad(GamepadPtr gp) {
bool foundEmptySlot = false;
for (int i = 0; i < BP32_MAX_GAMEPADS; i++) {
if (myGamepads[i] == nullptr) {
Serial.printf("CALLBACK: Gamepad is connected, index=%d\n", i);
// Additionally, you can get certain gamepad properties like:
// Model, VID, PID, BTAddr, flags, etc.
GamepadProperties properties = gp->getProperties();
Serial.printf("Gamepad model: %s, VID=0x%04x, PID=0x%04x\n", gp->getModelName().c_str(), properties.vendor_id,
properties.product_id);
myGamepads[i] = gp;
foundEmptySlot = true;
break;
}
}
if (!foundEmptySlot) {
Serial.println("CALLBACK: Gamepad connected, but could not found empty slot");
}
}


void onDisconnectedGamepad(GamepadPtr gp) {
bool foundGamepad = false;


for (int i = 0; i < BP32_MAX_GAMEPADS; i++) {
if (myGamepads[i] == gp) {
Serial.printf("CALLBACK: Gamepad is disconnected from index=%d\n", i);
myGamepads[i] = nullptr;
foundGamepad = true;
break;
}
}


if (!foundGamepad) {
Serial.println("CALLBACK: Gamepad disconnected, but not found in myGamepads");
}
}


// Arduino setup function. Runs in CPU 1
void setup() {
Serial.begin(115200);
Serial.printf("Firmware: %s\n", BP32.firmwareVersion());
const uint8_t* addr = BP32.localBdAddress();
Serial.printf("BD Addr: %2X:%2X:%2X:%2X:%2X:%2X\n", addr[0], addr[1], addr[2], addr[3], addr[4], addr[5]);


// Setup the Bluepad32 callbacks
BP32.setup(&onConnectedGamepad, &onDisconnectedGamepad);


// "forgetBluetoothKeys()" should be called when the user performs
// a "device factory reset", or similar.
// Calling "forgetBluetoothKeys" in setup() just as an example.
// Forgetting Bluetooth keys prevents "paired" gamepads to reconnect.
// But might also fix some connection / re-connection issues.
BP32.forgetBluetoothKeys();




// Enable-Pins dauerhaft HIGH
pinMode(L_EN, OUTPUT); digitalWrite(L_EN, HIGH);
pinMode(R_EN, OUTPUT); digitalWrite(R_EN, HIGH);
pinMode(R_L_EN, OUTPUT); digitalWrite(R_L_EN, HIGH);
pinMode(R_R_EN, OUTPUT); digitalWrite(R_R_EN, HIGH);


// LEDC-Kanäle binden
ledcSetup(CH_L_FWD, PWM_FREQ, PWM_RES);
ledcSetup(CH_L_BWD, PWM_FREQ, PWM_RES);
ledcSetup(CH_R_FWD, PWM_FREQ, PWM_RES);
ledcSetup(CH_R_BWD, PWM_FREQ, PWM_RES);


ledcAttachPin(L_PWM, CH_L_FWD);
ledcAttachPin(R_PWM_L, CH_L_BWD);
ledcAttachPin(R_L_PWM, CH_R_FWD);
ledcAttachPin(R_R_PWM, CH_R_BWD);
}


// Arduino loop function. Runs in CPU 1
void loop() {
// This call fetches all the gamepad info from the NINA (ESP32) module.
// Just call this function in your main loop.
// The gamepads pointer (the ones received in the callbacks) gets updated
// automatically.
BP32.update();


// It is safe to always do this before using the gamepad API.
// This guarantees that the gamepad is valid and connected.
for (int i = 0; i < BP32_MAX_GAMEPADS; i++) {
GamepadPtr myGamepad = myGamepads[i];


if (myGamepad && myGamepad->isConnected()) {
// There are different ways to query whether a button is pressed.
// By query each button individually:
// a(), b(), x(), y(), l1(), etc...
// ── Ersatz für den alten Block (Zeilen 79-117) im loop() ──


// Linker Motor → axisY() (negativ = Stick oben = vorwärts)
int leftY = myGamepad->axisY();
// Rechter Motor → axisRY() (negativ = Stick oben = vorwärts)
int rightY = -myGamepad->axisRY();


// ── Linker Motor ──
if (abs(leftY) < DEADZONE) {
// Deadzone: Motor stop
ledcWrite(CH_L_FWD, 0);
ledcWrite(CH_L_BWD, 0);
} else if (leftY < 0) {
// vorwärts: -10 bis -508
int speed = map(abs(leftY), DEADZONE, 508, 0, 255);
speed = constrain(speed, 0, 255);
ledcWrite(CH_L_FWD, speed);
ledcWrite(CH_L_BWD, 0);
} else {
// rückwärts: 10 bis 512
int speed = map(leftY, DEADZONE, 512, 0, 255);
speed = constrain(speed, 0, 255);
ledcWrite(CH_L_FWD, 0);
ledcWrite(CH_L_BWD, speed);
}



// ── Rechter Motor ──
if (abs(rightY) < DEADZONE) {
ledcWrite(CH_R_FWD, 0);
ledcWrite(CH_R_BWD, 0);
} else if (rightY < 0) {
// vorwärts: -10 bis -508
int speed = map(abs(rightY), DEADZONE, 508, 0, 255);
speed = constrain(speed, 0, 255);
ledcWrite(CH_R_FWD, speed);
ledcWrite(CH_R_BWD, 0);
} else {
// rückwärts: 10 bis 512
int speed = map(rightY, DEADZONE, 512, 0, 255);
speed = constrain(speed, 0, 255);
ledcWrite(CH_R_FWD, 0);
ledcWrite(CH_R_BWD, speed);
}


// Another way to query the buttons, is by calling buttons(), or
// miscButtons() which return a bitmask.
// Some gamepads also have DPAD, axis and more.
Serial.printf(
"idx=%d, dpad: 0x%02x, buttons: 0x%04x, axis L: %4d, %4d, axis R: %4d, "
"%4d, brake: %4d, throttle: %4d, misc: 0x%02x\n",
i, // Gamepad Index
myGamepad->dpad(), // DPAD
myGamepad->buttons(), // bitmask of pressed buttons
myGamepad->axisX(), // (-511 - 512) left X Axis
myGamepad->axisY(), // (-511 - 512) left Y axis
myGamepad->axisRX(), // (-511 - 512) right X axis
myGamepad->axisRY(), // (-511 - 512) right Y axis
myGamepad->brake(), // (0 - 1023): brake button
myGamepad->throttle(), // (0 - 1023): throttle (AKA gas) button
myGamepad->miscButtons() // bitmak of pressed "misc" buttons
);


// You can query the axis and other properties as well. See Gamepad.h
// For all the available functions.
}
}


// The main loop must have some kind of "yield to lower priority task" event.
// Otherwise the watchdog will get triggered.
// If your main loop doesn't have one, just add a simple `vTaskDelay(1)`.
// Detailed info here:
// https://stackoverflow.com/questions/66278271/task-watchdog-got-tri ggered-the-tasks-did-not-reset-the-watchdog-in-time


// vTaskDelay(1);
delay(20);
}

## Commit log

2026-02-12 freecad- und notizen-datei
    [rahmen.FCStd]
2026-02-12 ordner für 3D-Druck
    [rahmen.FCStd]
2026-02-13 Änderungen
    [rahmen.FCStd]
2026-02-13 Add Kugellager und Achsen to README
2026-02-16 neue 3d-Dateien
    [rahmen.FCStd, rahmen_neu.FCStd, triebrad-Rad.stl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]
2026-02-16 neue stl-test datei für das Triebrad
    [triebrad-Rad_neu.stl, triebrad.FCStd]
2026-02-16 neue Rahmen-datei
    [rahmen.FCStd, rahmen_neu.FCStd]
2026-02-19 neues 3d-modell für plattform + stl-datei
    [rahmen-platte.stl, rahmen.FCStd]
2026-02-20 neue 3d-modelle
    [brett.FCStd, rahmen.FCStd, triebrad.FCStd]
2026-02-23 neue stl-datei für plattform
    [rahmen.FCStd, rahmen_neu.stl]
2026-02-23 neue 3D-Dateien (Rahmen)
    [rahmen.FCStd, rahmen_neu_2.stl]
2026-02-26 neue 3d-dateien für Grundplatte
    [rahmen.FCStd, rahmen_alt.stl, rahmen_neu.3mf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]
2026-02-27 Rahmen überarbeitet; bis auf Hinterrad und Steckmechanismus fertig
    [rahmen_neu.FCStd]
2026-02-27 FreeCAD- und STL-Datei für ESP32-Halterung erstellt
    [esp32_halterung.FCStd, esp32_halterung.stl, rahmen_neu.FCStd]
2026-03-03 Rahmen-Modell überarbeitet
    [rahmen_neu.FCStd, test_halterung.FCStd]
2026-03-07 Add ESP32 gamepad connection handling code
2026-03-16 3d-dateien geändert
    [achse_halterung.stl, achse_halterung_315.stl, block.FCStd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]
2026-03-20 Change PWM values for left and right motor
    Updated PWM values for motor control to increase speed.
2026-03-22 Äußere Stütze für vorderes Rad erstellt + STL-Datei, ggf. Höhe anpassen
    [stütz_scheibe_vorne.FCStd, stützrad_außen.FCStd, stützrad_außen.stl]
